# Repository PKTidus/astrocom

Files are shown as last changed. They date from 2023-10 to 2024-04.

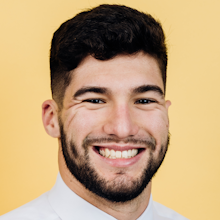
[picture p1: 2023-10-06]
software/website/img/stephen.png

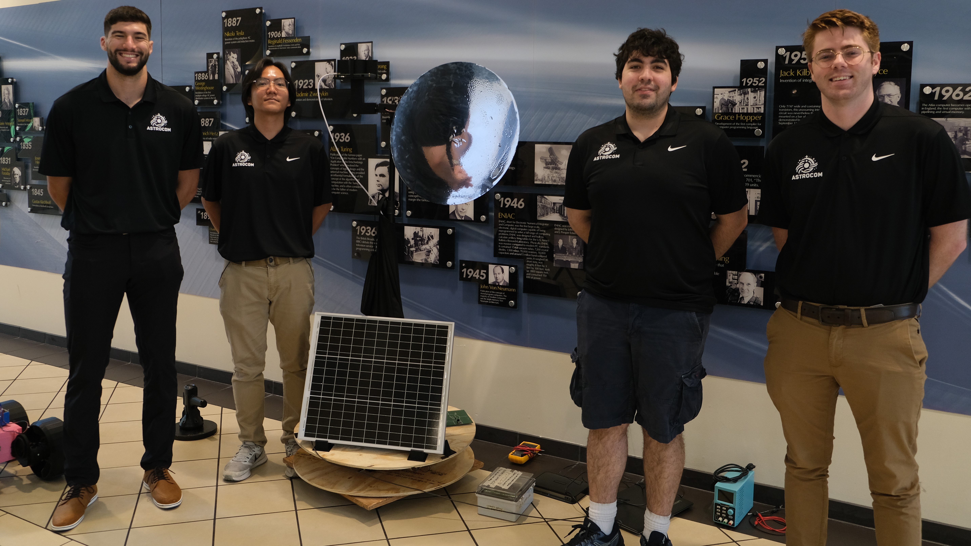
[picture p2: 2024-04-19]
software/website/img/demo_day_pic.jpg

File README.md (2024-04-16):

# A.S.T.R.O.COM. - Advanced Solar Tracking and Rover Observation Communication

The ASTROCOM project, developed in collaboration with the [Florida Space Institute (FSI)](https://fsi.ucf.edu/), addresses the challenge of exploring permanently shaded regions on the lunar surface. Comprising of heliostat and communication beacon towers, ASTROCOM enables wireless transmission of power and information to and from rovers within these shaded areas. The Heliostat tower utilize a reflector to redirect sunlight into the craters, powering solar assets and illuminating shaded regions, while also enabling a communication network. A portable communication beacon, intended to be deployed by rovers, a facilitate communication between the heliostat towers and rovers, overcoming obstacles within the craters.
Heliostat Tower             |  Communication Beacon
:-------------------------:|:-------------------------:
Heliostat Tower CAD  |  Communication Beacon CAD

**Project Members:**  
Alex Fiset (Power/PCB)  
Pedro Kasprzykowski (Wireless/Website)  
Stephen Martin (Sensors/Solar Tracking)  
Binh Pham (Project Lead/Motors)  

**Special Thanks:**  
Dr. Chung Yong Chan  
Dr. Arthur Weeks  

**This project was sponsored by the [Florida Space Institute](https://fsi.ucf.edu/)**  

**This project was made as a [University of Central Florida Electrical and Computer Engineering Department](https://www.ece.ucf.edu/) Senior Design project throughout the Fall 2023 - Spring 2024 term**

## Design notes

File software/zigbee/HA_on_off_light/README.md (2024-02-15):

| Supported Targets | ESP32-C6 | ESP32-H2 |
| --- | --- | --- |

# Light Bulb Example

This test code shows how to configure Zigbee end device and use it as HA on/off light bulb.

The ESP Zigbee SDK provides more examples and tools for productization:
* [ESP Zigbee SDK Docs](https://docs.espressif.com/projects/esp-zigbee-sdk)
* [ESP Zigbee SDK Repo](https://github.com/espressif/esp-zigbee-sdk)

## Hardware Required

* One development board with ESP32-H2 SoC acting as Zigbee end device (loaded with HA_on_off_light example)
* A USB cable for power supply and programming
* Choose another ESP32-H2 as Zigbee coordinator (see [HA_on_off_switch example](../HA_on_off_switch))

## Configure the project

Before project configuration and build, make sure to set the correct chip target using `idf.py --preview set-target TARGET` command.

## Erase the NVRAM

Before flash it to the board, it is recommended to erase NVRAM if user doesn't want to keep the previous examples or other projects stored info using `idf.py -p PORT erase-flash`

## Build and Flash

Build the project, flash it to the board, and start the monitor tool to view the serial output by running `idf.py -p PORT flash monitor`.

(To exit the serial monitor, type ``Ctrl-]``.)

## Example Output

As you run the example, you will see the following log:

light bulb:
```
I (918) ESP_ZB_LIGHT: status: 255
I (901) ESP_ZB_LIGHT: Zigbee stack initialized
I (901) ESP_ZB_LIGHT: Start network steering
I (2611) ESP_ZB_LIGHT: Joined network successfully (Extended PAN ID: aa:98:48:01:a0:03:f7:84, PAN ID: 0x0e8b)
I (5651) ESP_ZB_LIGHT: on/off light set to 1
I (6631) ESP_ZB_LIGHT: on/off light set to 0
I (7331) ESP_ZB_LIGHT: on/off light set to 1
I (8251) ESP_ZB_LIGHT: on/off light set to 0
I (9111) ESP_ZB_LIGHT: on/off light set to 1
I (9671) ESP_ZB_LIGHT: on/off light set to 0
```

## Light Control Functions

 * By toggling the switch button (BOOT) on the ESP32-H2 board loaded with the `HA_on_off_switch` example, the LED on this board loaded with `HA_on_off_light` example will be on and off.

## Troubleshooting

For any technical queries, please open an [issue](https://github.com/espressif/esp-idf/issues) on GitHub. We will get back to you soon.

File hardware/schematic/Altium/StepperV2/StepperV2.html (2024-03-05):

Altium customize

# Board Information Report

Date: | | 2/26/2024
Time: | | 11:22:44 AM
Elapsed Time: | | 00:00:00
Filename: | | C:\Users\binhp\OneDrive\Desktop\Working\School\Senior_Design\Github\astroscom\hardware\schematic\Altium\StepperV2\StepperV2.PcbDoc
Units: | | mmmils

## Contents

Contents

Board Specification

General

## Board Specification

General
Board Size | 4995mils x 4000mils
Components on board | 58

Back to top

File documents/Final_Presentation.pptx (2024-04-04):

## A.S.T.R.O.COM. Advanced Solar Tracking and Rover Observation Communication

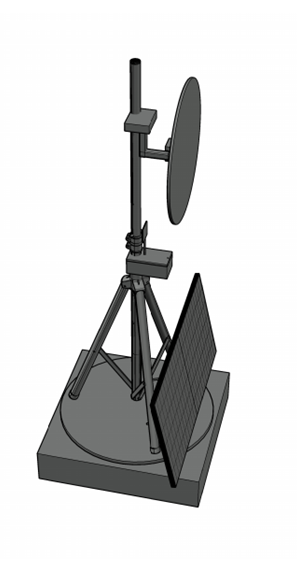
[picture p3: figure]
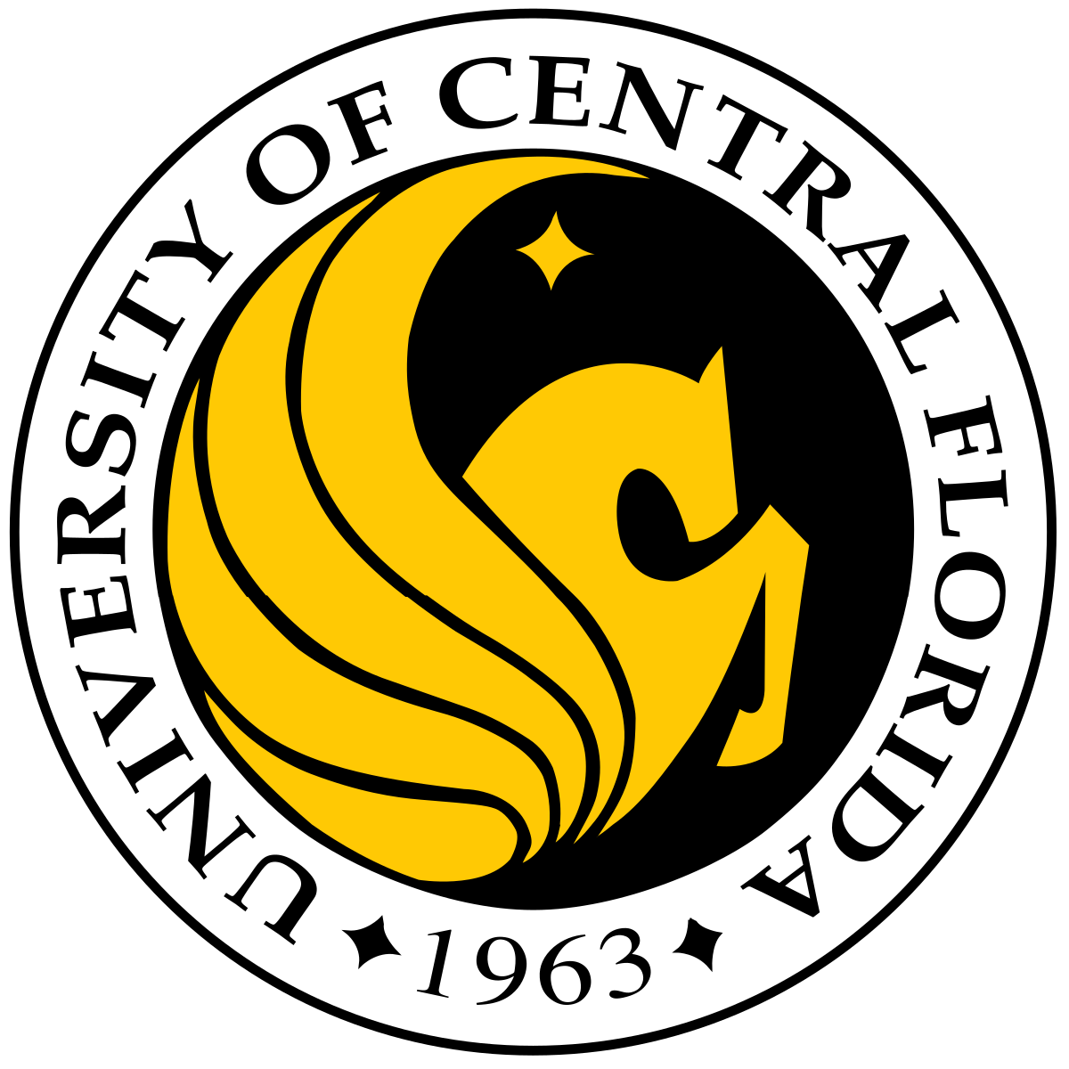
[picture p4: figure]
University of Central Florida - Wikipedia

Alex Fiset | Pedro Kasprzykowski | Stephen Martin | Binh Pham
Electrical Engineering | Computer Engineering | Computer Engineering | Computer Engineering

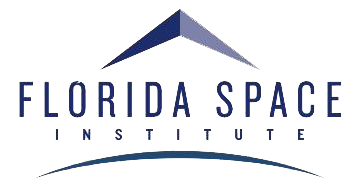
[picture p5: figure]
Florida Space Institute - Wikipedia

Project sponsored by Florida Space Institute (FSI)

## Motivation and Background

- South Pole of Moon is area of interest for researchers
- Lunar south pole has many craters that are in permanent darkness due to the sun's path across the lunar south pole's sky
- Approached by FSI to solve a few problems for lunar exploration:
  1. Permanently dark locations on the moon are difficult to explore
    - Lack of power infrastructure on the moon limits exploration
    - Permanently dark locations are a valuable location for research
  2. Communication on lunar surface is limited
    - Range of communication limits exploration of craters
    - Limited communication infrastructure on moon

## Motivation and Background

- Proposed Solution:
  1. A heliostat tower
    - To reflect light from the sun into permanently dark locations
    - Equipped with communication capabilities
  2. A smaller communication beacon
    - Carriable by rovers
    - Form a communication network with rovers

## Goals

Overall Goals (High Level)
- Build a tower to handle rover communication.
- Build a tower to handle sunlight diversion to targets.
Stretch Goals
- P2P Networking for communication and mirror tower with rovers.
- Wireless charging and/or docking station for communication tower.

## Objectives

Mirror Tower Objectives (Lower Level)
- Identify optimal sun location based on lux value from sensor.
- Receive requests from communication tower using protocols.
- Create a heliostat algorithm to orient towards the target with motors.
- Create a self-sustainable power supply using solar and battery power.
Communication Beacon Objectives (Lower Level)
- Receive requests from target through mesh network protocols.
- Relay requests to mirror tower using communication protocols.
- Create a small and portable tower that can be moved by rovers.

## Specifications Table

Heliostat Tower
Minimum Temperature | -40°C
Reflector
Minimum Reflectivity | 90%
Response Time | 3 minutes
Solar Panel
Minimum Power | 30W during sunlight hours
Maximum Voltage | 24V
Battery
Minimum Lifespan | 2 weeks without sun

Communication Tower
Minimum Network Range | 20m
Communication Rate | 2400MHz
Maximum Current Draw | 500mA
Latency | 1 second
Maximum Power | 5W

  1. A heliostat tower
    - Respond time to change reflection target estimated to be maximum 3 minutes
    - Minimum power can be usage to all component estimated to be 30W
  2. Communication tower
    - Maximum power usage estimated to be 5W

## Hardware Block Diagram

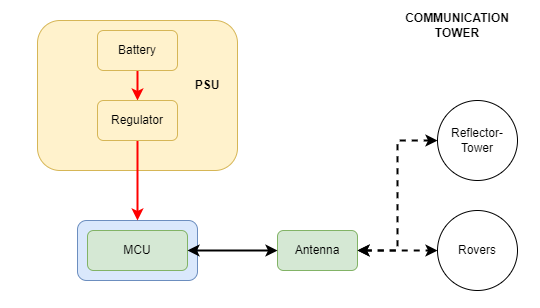
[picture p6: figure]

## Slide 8

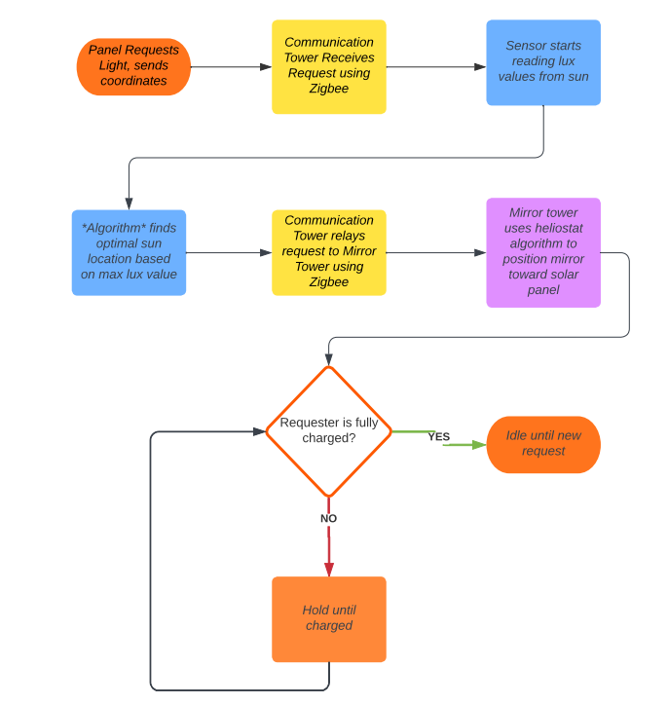
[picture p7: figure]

Software
Block
Diagram

- Fully integrated code software flowchart
  - Perspective of Mirror Tower
  - Yellow is signal from Communication Beacon

## MICROCONTROLLER UNIT

| ESP32 | MSP430 | Raspberry Pi 0 | Arduino MKR1310 | Arduino MK1010
Cost (USD) | 9.18 | 20 | 15 | 46 | 38.6
Zigbee | Yes | No | Yes | No | No
I2C | Yes | Yes | Yes | Yes | Yes
Flash Memory | 4 MB | 128 KB | None | 256 KB | 256 KB
RAM | 520 KB | 2 KB | 512 MB | 32 KB | 32 KB
Power (W) | 1.3644 | 1 | 12.5 | 0.5082 | 0.5082

- Microcontroller was chosen over FPGA
  - Low power consumption, cost, and high amounts of documentation.
- ESP32 is low cost, low power and networking capabilities and all connections required.

## Solar Panels

A monocrystalline 50W panel from Renogy was selected due to the low cost and high performance.

Model | RNG-50D-SS | HQST-50P-US | SP-52-L
Brand | Renogy | HQST | Solbian
Technology | Monocrystalline | Polycrystalline | Monocrystalline
Price | $ 59.99 | $ 65.99 | $ 499.00
Pmax at STC | 50 W | 50 W | 52 W
Voc | 22.3V | 23.3V | 10.9V
Vmp | 18.6V | 19.8V | 9.1V
Imp | 2.69A | 2.53A | 5.7A

## Voltage Regulation

Specifications | Linear Regulators | Switching Regulators
| | Buck | Boost | Buck-Boost
Efficiency | Moderate | High
Heat | Moderate | Low
Voltage Output | Step-Down | Step-Down | Step-Up | Up or Down
Output Ripple | Low | Low | High | Low
Complexity | Low | Moderate | Moderate | High
Cost | Low | Moderate | Moderate | High

Switching Buck regulators were chosen for their simplicity and low cost, being commercially available cheaply from many manufacturers.

## Voltage Regulation

The TPS53JA2 was selected due to the high output current, supported the intended voltage input, and was high efficiency.

Model | LM1085IT-5.0/NOPB | DROK MiniBuck Converter | LM2596 | TPS54JA20
Brand | Texas Instruments | DROK | Texas Instruments | Texas Instruments
Input Voltage | 2.6-26V | 2.5-24V | 3-40V | 2.7–16V
Output Voltage | 3.3 or 5 | 3.3 or 5 | 1.5 to 35 | 0.5 to 5.5V
Output Current | 3A | 3A | 3A | 12A
Price | 2.19 | 1.97 | 1.495 | 0.65
Type | LDO Buck | Buck | Buck | Buck

## Charge Controller

- Two broad categories of Solar Charge Controllers:
  1. PWM
    - Basic pulse width modulation
    - Lower efficiency
    - Cheaper
  2. MPPT
    - Tracks highest power producing operating point
    - Higher efficiency
    - Typically, more expensive

## Charge Controller

The SR11004 from SMARAAD offered the right voltage output, and was compatible with the selected battery chemistry for the lowest price.

Model | BQ25798RQMR | SR11004 | Adventurer
Brand | Texas Instruments | SMARAAD | Renogy
Input Voltage | 24V max | 26V max | 50V max
Output Voltage | 18.8V max, Programmable | 12/24V | 12/24V
Output Current | 5A | 10A | 30A
Price | 6.25 | 39.99 | 59.99
Power | Not Specified | 260W | 1500W
Type | MPPT | MPPT | PWM

## Reflectors

- Material Chosen to fabricate:
1. Aluminum: high heat resistance, durable, and high reflectivity in the moon environment.
2. Mylar: increase reflectivity, high heat change resistance, won’t crack, and don’t reduce quality of refection
- Proof of concept: Acrylic panel as cheaper alternative and easier to fabricate.

## Motors

1. Stepper motor: Nema 23 robustness and strong torque to control the rotation of the whole tower. Can be used on DC system
2. Servo Motors: a cheaper alternative for smaller part movements.
- Incorporated gearbox to increase movement range and control for stepper motor.

Types of Motors | AC | Stepper | Servo
Financial Cost | $200-$2,000 | $20-$200 | $10-$50
Torque | 203000Ncm-610000Ncm | 10-10000Ncm | 10-1000Ncm
Speed | 1800-3600 rmp | Low | High
Voltages requirement | 115V/208V/230V | 3V-100V | 3V-100V
Durability | High | High | Low

## Motor Controllers

1. Stepper Controller TB6560-V2, cheap and can handle the at least 2 amperage from Nema23
2. PCA9685 PWM: Design specific for servo and can control all three servos planned in the system

Controller Models | DRV8434S, 2A Max. | TB6560 | Stepper Motor Driver 36v4 | HiLetgo PCA9685
Cost (USD) | $12.95 | $11.39 | $29.95 | $9
continuous current (A) | 1.2 | 3.5 | 4 | 3A
Micro stepping | 1/256 | 1/16 | 1/256 | I2C
Operating Voltage (V) | 4.5-48 | 10-35 | 8-50 | 5-10

## Batteries

- The battery selected was a Howell Energy LiFePO4 battery.
  - Higher amp hours
  - Lower weight
  - Smaller size
  - Higher price

Model | ML5-12 | HW-4F7 | PQ12V/6AH
Brand | Mighty Max Battery | Howell Energy | Power Queen
Voltage | 12 | 12 | 12.8V
Amp Hour | 5 | 7 | 6
Technology | SLA AGM | LiFePO4 | LiFePO4
Price | 16.99 | 32.99 | 19.59
Charging Requirements | CV | CC 3.5A, CV 14.6V, Built-in BMS | Not Specified, Built in BMS

## Antenna

- The combination of the certain gain range, circular polarization, high-efficiency and wideband characteristics made patch and helical antenna types the ideal choices.
- The PC140’s circular polarization while also being above average in gain and efficiency made it the preferred antenna product.
- The sponsor chose for us to replace the antenna with their choice of the wlaniot.

| PC140 | WPC.25A | FXP74 | PC17 | FXP70
Avg Gain (dB) | -1.92 | -1.14 | -2 | -3.6 | -2
Peak Gain (dBi) | 1.67 | 5.15 | 4 | .9 | 1.1
Efficiency (%) | 64 | 76.9 | 50 | 44 | 63.7
VSWR | <2 | <2 | <2 | <1.5 | <1.5
Polarization | RHCP | Linear | Linear | Linear | Linear
Cost (USD) | $27.26 | $9.21 | $7.69 | $16.60 | $27.09

## Sensor

Sensor Final 4 Options:
- VL6180X and SI1145 include IR which is not needed
- MAX44009 only has breakout board; does not work for PCB
- VEML7700 best choice for price/ability

| VL6180X | MAX44009 | SI1145 | VEML7700
Cost (USD) | $14.49 | $5.96 | $9.95 | $4.95
Measuring Principle | TOF/IR Laser Photodiode | Photodiode | IR-LED Photodiode | Photodiode
Max Lux | 100000 | 188000 | 128000 | 120000
Ambient Light Sensing | Yes | Yes | Yes | Yes
Operating Current (mA) | 0.3 | 0.003 | 7 | 0.045
I2C | Yes | Yes | Yes | Yes

## Development Environment: Languages and Repositories

Programming Languages
- C: best choice for MCU programming, low-level
- Java: best for object-oriented programming, low-level
- Python: best for existing libraries, high-level
Choice: C
Repositories
- GitHub: most popular repo, widely used among many software devs
- Bitbucket: Git based repo, includes task scheduling and team goal software
Choice: GitHub

## Vectoring and Positioning / Solar Tracking Algorithm

1. Heliostat algorithm chosen as it is open source and availability. Good capability with ESP32-C6 and C language

Algorithms | Heliostat | Kalman Filtering | Ray Tracing
Financial Cost | Open Source | Ambiguous | Not available
Sensor | Ambient Light | Ambient Light | Ambient Light
Algorithm code library | Available on GitHub | Available in python | Available in Research paper
Efficiency | High | Low | Medium
MCU compatibility | Good (C Language) | Fair (Python) | Good (C Language)

## Communication technologies

- The combination of low power consumption, suitable range, options for frequency and high scalability made Zigbee the ideal communication technology to implement.

Criteria | Wi-Fi | Bluetooth | Zigbee | Z-Wave
Range (m) | 45 | 10 | 980 | 800
Data rate | 54 Mbps | 1 Mbps | 250 Kbps | 100 Kbps
Power consumption | 30 uA-250 mA | 9 uA-39 mA | 12 uA- 54 mA | 1 uA-23 mA
Max devices | 255 | 3-4 | 100 | 232
Scalability | ✓ | ✖ | ✓ | ✓
Frequency | 2.4/5/6 GHz | 2.4 GHz | 915 MHz/2.4 GHz | 908-916 MHz

## Hardware Design

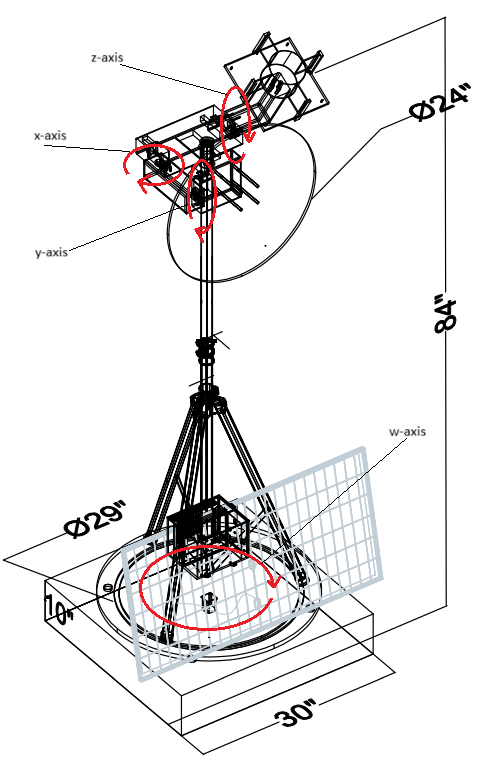
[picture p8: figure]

- Design two separate towers, each with their own design constraints
- Majority of focus is on heliostat tower, as it is more complex
- Schematics and PCB designs
- Heliostat structure
- Tripod on a "Lazy Susan"
- Communication Beacon
- Antenna on an enclosure

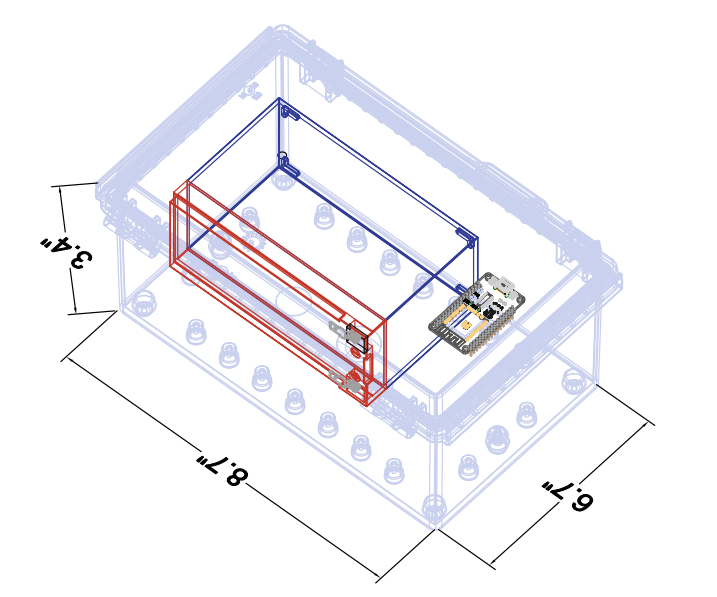
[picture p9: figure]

## Power Delivery/ Electrical Power System

## Servo Motor Controls

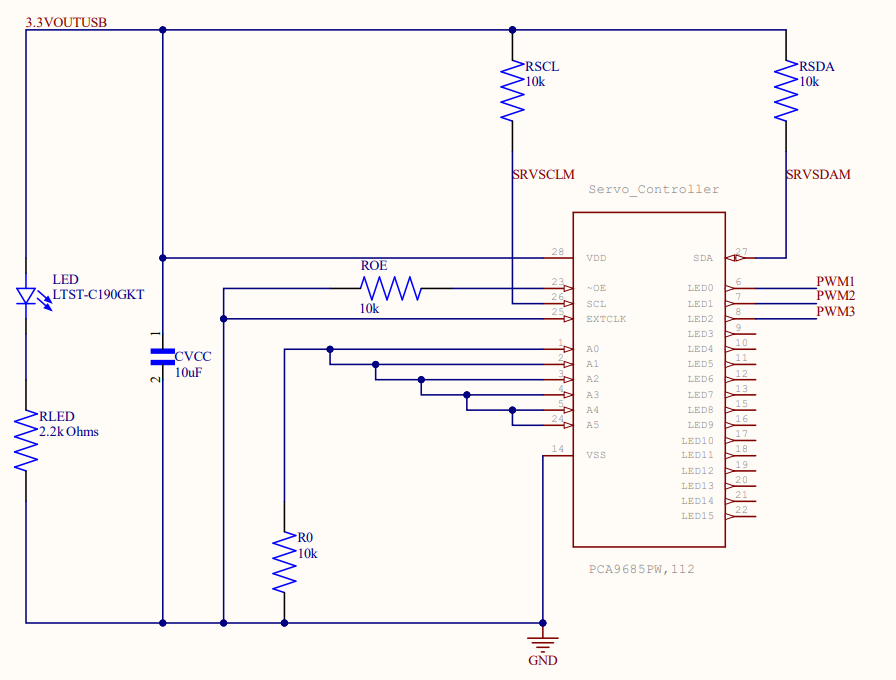
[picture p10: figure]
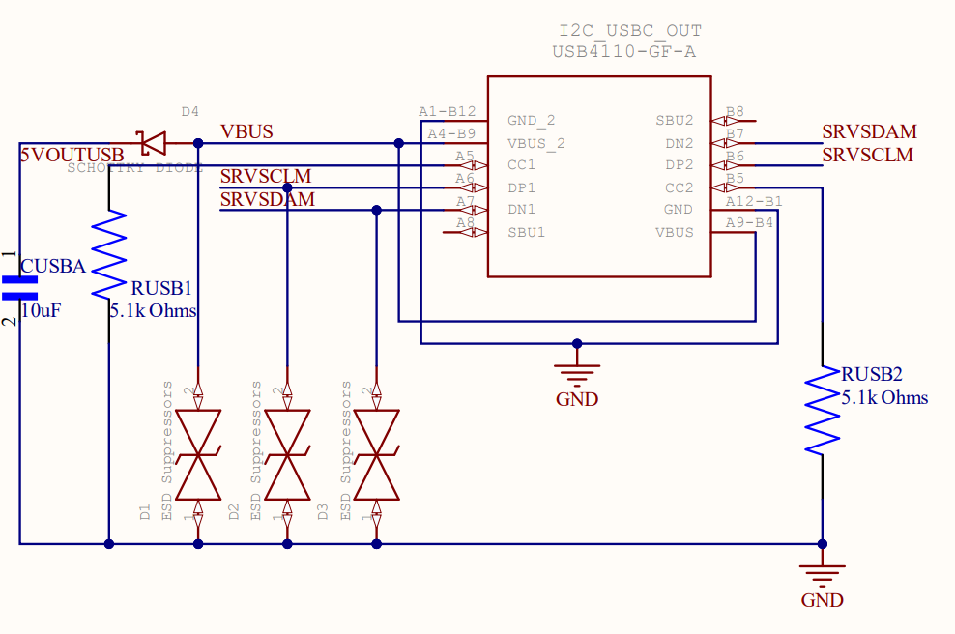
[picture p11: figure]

## Sensor Control

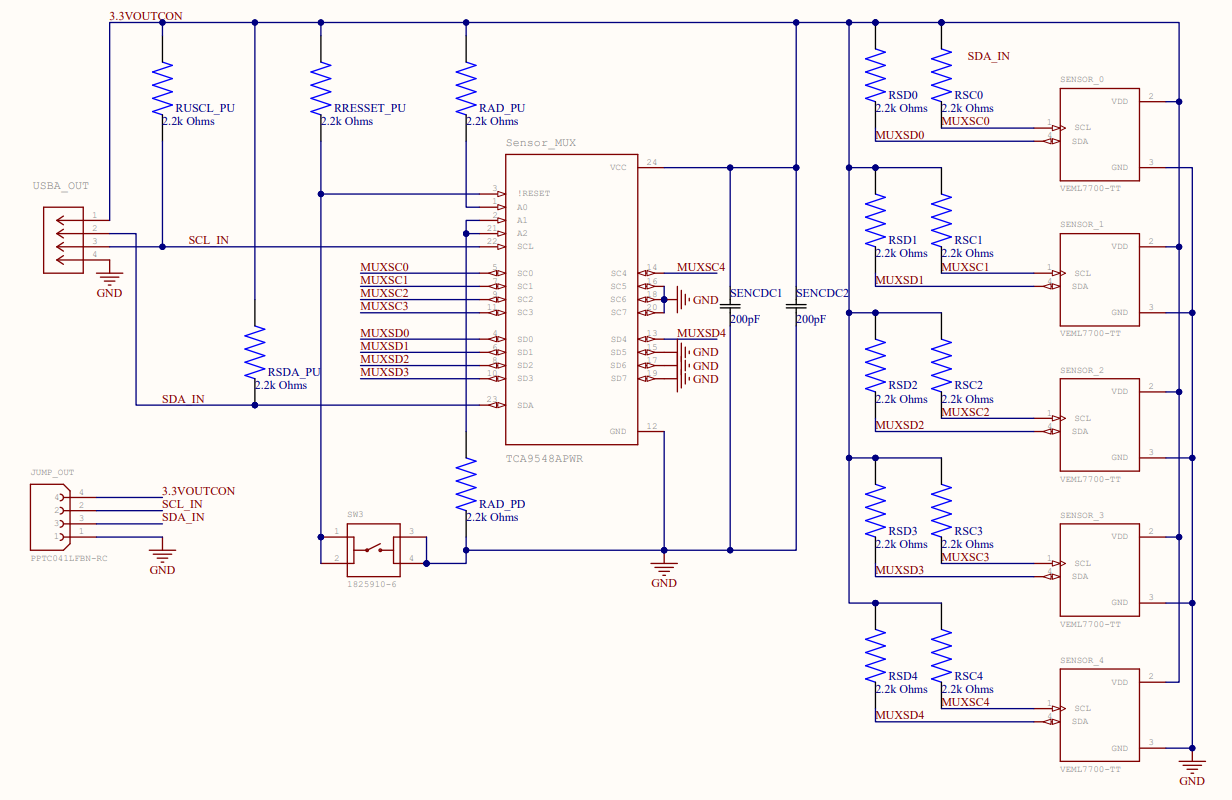
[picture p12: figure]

## MCU System

## Lower-Level Subsystem

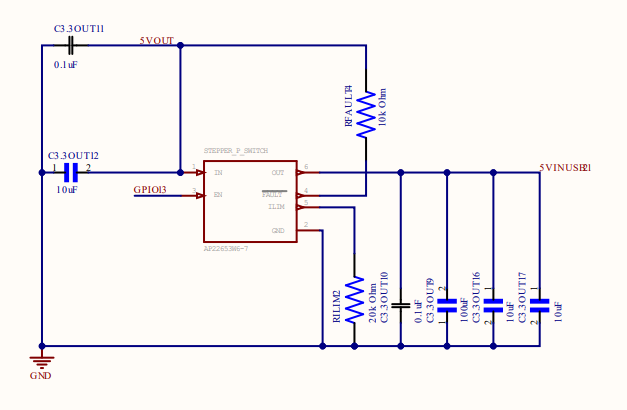
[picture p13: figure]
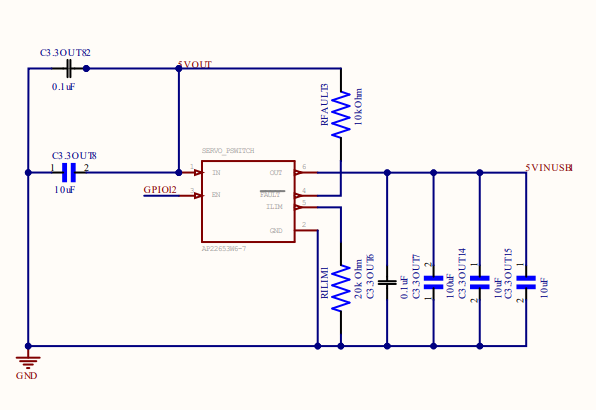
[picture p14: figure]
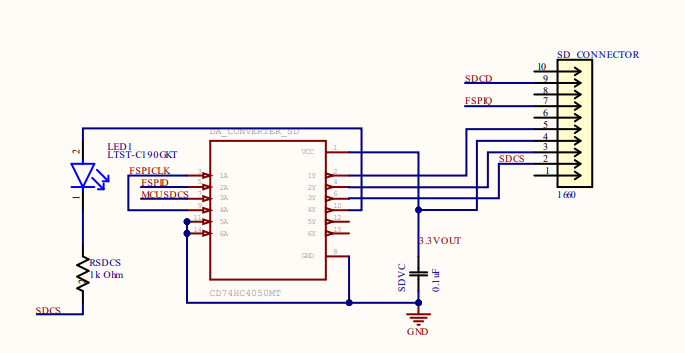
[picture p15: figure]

## Lower-Level Subsystem

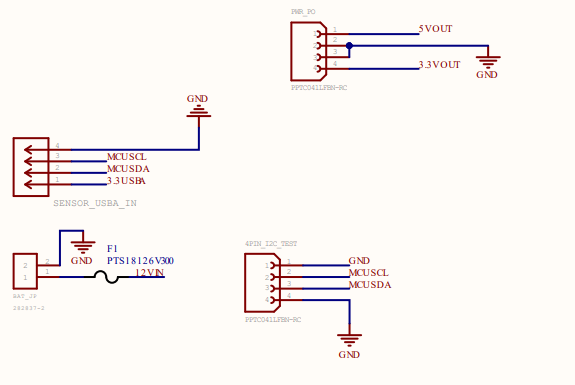
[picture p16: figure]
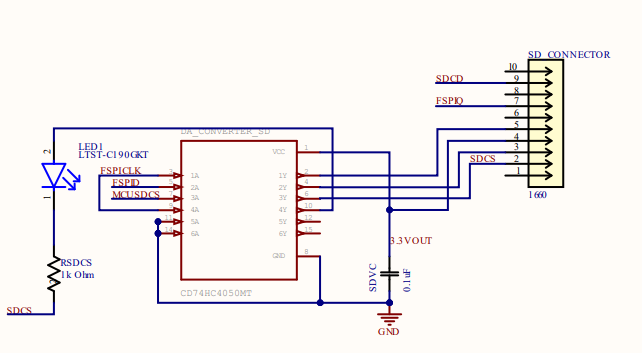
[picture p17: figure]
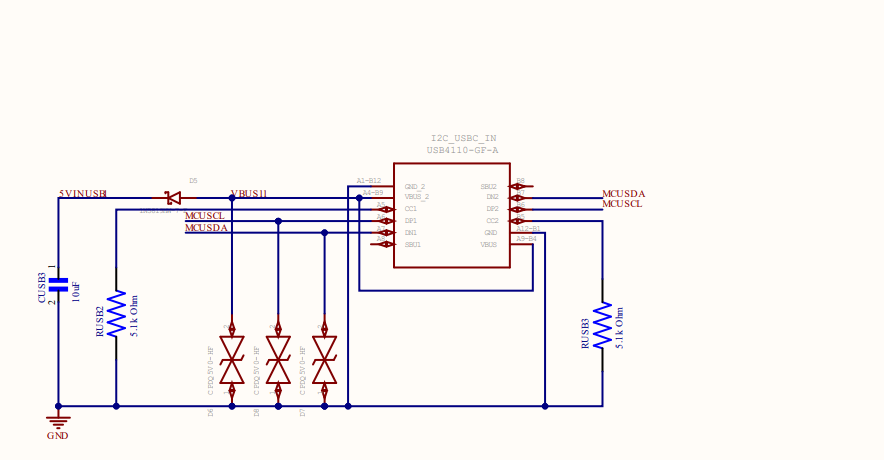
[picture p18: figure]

## Power Control Algorithm

Component | Essential/Non-Essential | Low-Power Considerations
MCU | Essential | Low-Power Mode, only essential functions
Antenna | Essential | Receive only
Sensors | Essential | Sensors will be turned on periodically
Stepper Motor | Non-Essential
Servo Motors | Non-Essential

- Goal was to reduce power consumption when the sun would not be visible
- Reducing usage of non-essential components during these times would preserve battery charge

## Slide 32

MCU PCB

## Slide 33

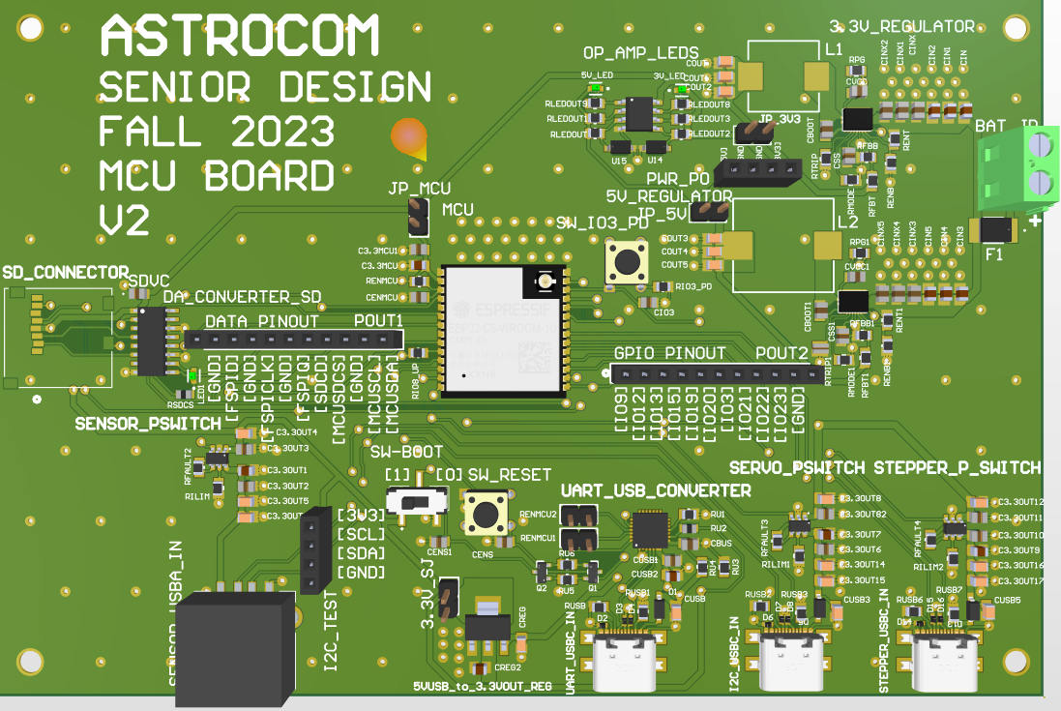
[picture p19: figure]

MCU PCB

## Sensors PCB

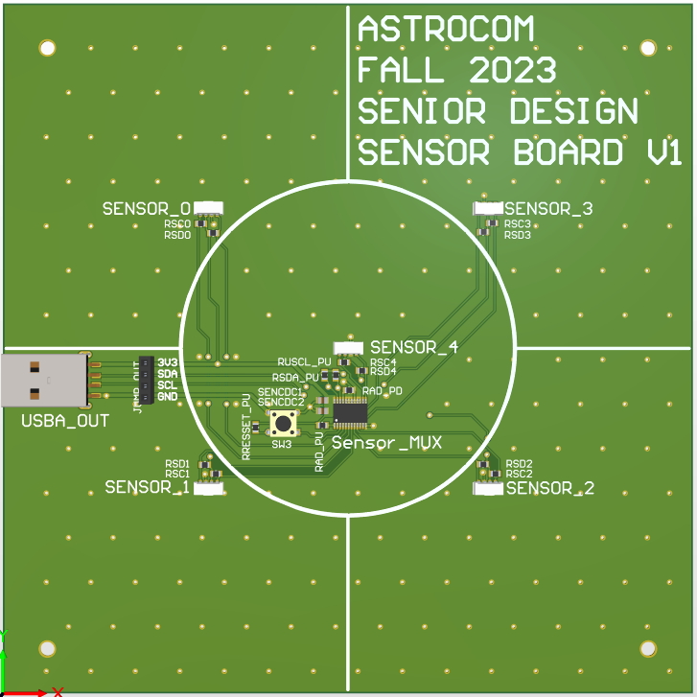
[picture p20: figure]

## SErVo Motor controller PCB

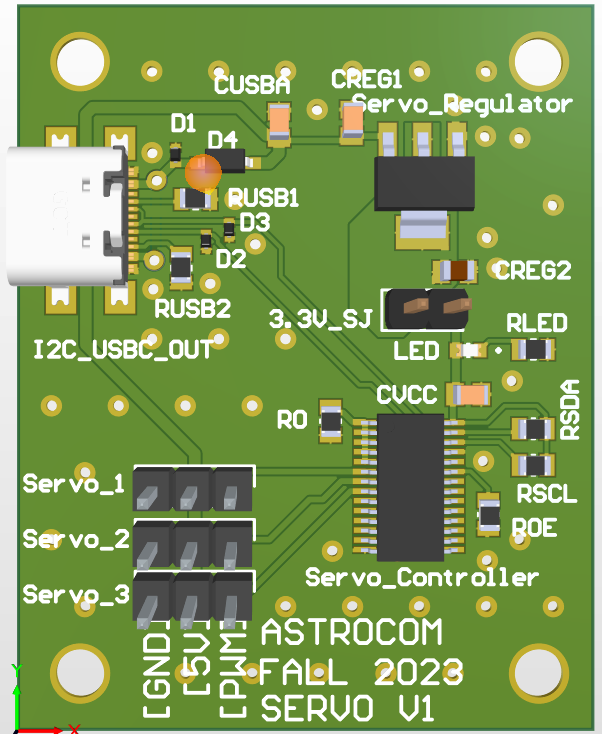
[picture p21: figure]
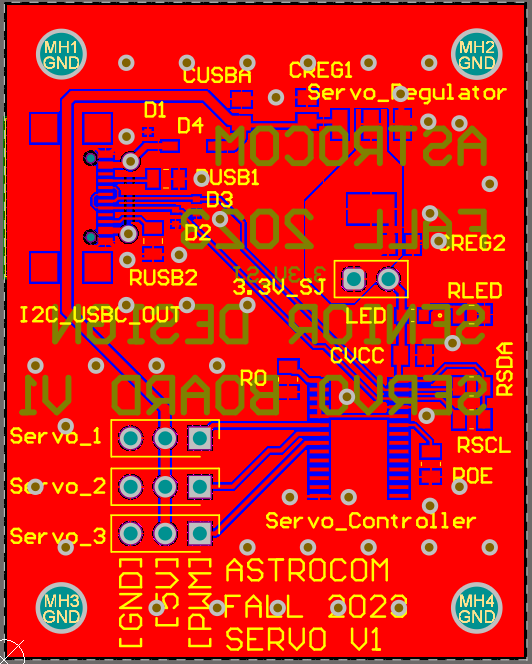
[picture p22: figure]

## Software Design

- Details on software design for the overall system which includes:
- Communications through the mesh network
- Collecting sensor information
- Positioning reflector to deliver sunlight to target
- Represented with software diagrams

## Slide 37

Case
Diagram

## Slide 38

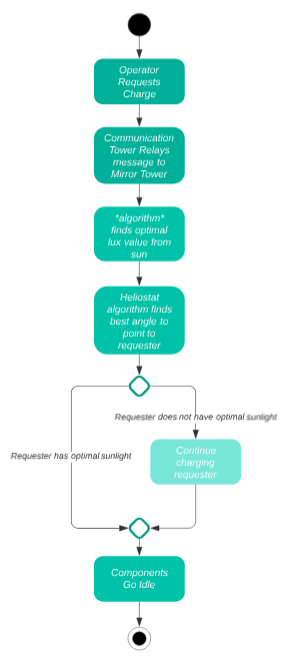
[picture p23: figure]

Activity Diagram

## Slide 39

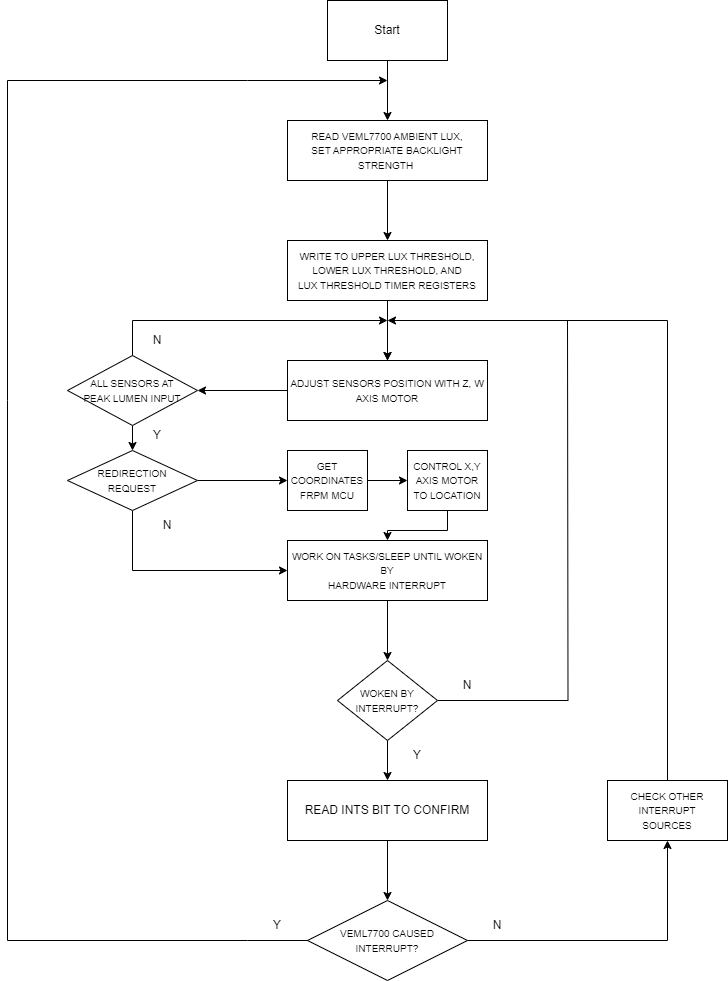
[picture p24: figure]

Motor positioning of Reflector based on light intensity algorithm.

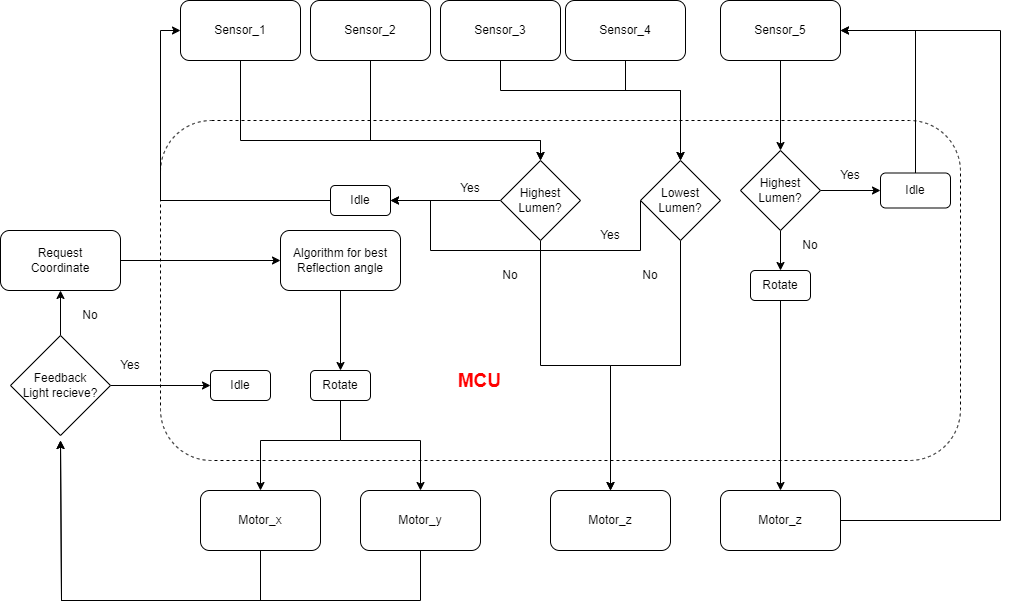
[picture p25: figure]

## Hardware testing

- Tested components and had great success.
- Did have a few issues during implementation including:
  - Strapping pins and UART TX/RX mix-ups
  - Higher than expected channel capacitance causing low rise time for I²C
  - Voltage drop from servos, resetting the servo controller
- These issues were resolved with a mix of software and hardware changes.

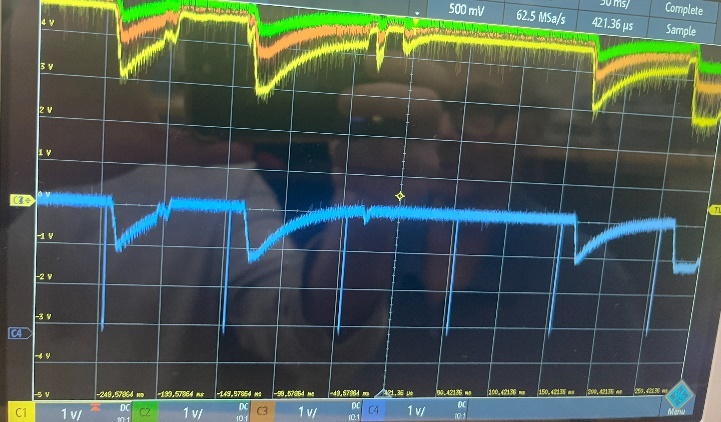
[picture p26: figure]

## Software testing

- Transforming individual parts code to integrated code
  - Included interrupts to handle events
  - Sensors in certain locations are averaged and divided by each other to dynamically track movements
  - Scaling operations were needed to transform step sizes from different servos
  - Zigbee operations included to switch targets
- Created our own coordinator for testing but will use rover from G16 in live demo
  - This coordinator will relay information from communication box (Zigbee end device) to the reflector tower (Zigbee end device)

## Administrative Contents

Electrical Engineering | Responsibilities
Alexandre Fiset | PSU Design and Implementation
| PCB Design
| MPPT Tracking Implementation
| Administrative Documentation
Computer Engineering | Responsibilities
Binh Pham | Reflector Technology and Design
| Motor and Motor Controls
| Vectoring Technology
| Project Lead
| Positioning and Vectoring Algorithm
Computer Engineering | Responsibilities
Pedro Kasprzykowski | MCU Selection and Implementation
| Software Design and Implementation
| Antenna and Communications
| Website Design and Management
Computer Engineering | Responsibilities
Stephen Martin | Sensor Selection and Implementation
| MCU Selection and Implementation
| Positioning and Vectoring Algorithm
| Software Design and Implementation

## Mechanical's Budgets

Component | Name | Price/unit | Quantity
Mirror | 0.032" x 24" x 24", 3003-H14 Aluminum Sheet | $28.86 | 1
Mirror Coating | Mylar Sheet | $25.99 | 1
Frame | ADJ LTS-6 T-Bar Tripod Lightweight Lighting Stand | $54.99 | 1
Base Panels | Plywood Panels 4ftx8ft | $25.60 | 2
Communication Tower Box | Junction Box | $26.89 | 1
Wheel Hub Bearing | Rear Wheel Hub | $44.90 | 1

## Electrical’s Budget

Component | Name | Price | Quantity
Battery | Howell Energy hw-4f7 | 32.99 | 1
Motor w | Nema 23 | $30.73 | 1
Motor x-y-z | 9.5-11kg*cm Servo Motor | $17.59 | 3
Charge Controller/BMS | Smaraad SR11004 | $39.99 | 1
Solar Panel | RNG-50D-SS | $49.99 | 1
Microcontroller | ESP32-C6-DEVKITC-1-N8 | $9.00 | 1
External Antenna | Wlaniot 2.4G | $17.98 | 2
MicroSD card | 5251 | $4.50 | 2
MicroSD card breakout board+ | 254 | $7.50 | 1

## PCB’s Budget

Component | Name | Price | Quantity
Microcontroller for PCB | ESP32-C6-WROOM-1U | $3.48 | 1
Stepper Motor Controller | DRV8833PW | $2.84 | 1
Servos Motor Controller | PCA9685PW,112 | $2.64 | 1
3.3V Regulator | TPS54JA20 | $1.50 | 1
5V Regulator | TPS54JA20 | $1.50 | 1
USB-A Connector | 2057-USB-AP-S-RA-SMT-ND | $0.55 | 3
Sensor-MUX | TCA9548APWR | $1.78 | 1
Sensor | VEML7700 | $1.88 | 5
USB-to-UART Bridge Controller | CP2102N-A02-GQFN28 | $4.07 | 1
MicroSD Socket | 1660 | $1.95 | 1
Misc. | Resistors, Capacitors, Inductr, Jumpers, Etc.…. | ~$20.00

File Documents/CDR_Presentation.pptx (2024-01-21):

## A.S.T.R.O.COM. Advanced Solar Tracking and Rover Observation Communication

Group 14’s
Members:


Alex Fiset | Pedro Kasprzykowski | Stephen Martin | Binh Pham
Electrical Engineering | Computer Engineering | Computer Engineering | Computer Engineering

## Motivation and Background

## Goals & Objectives

## Specifications Table

Heliostat Tower
Minimum Temperature | -40°C
Reflector
Minimum size | 1ft diameter
Maximum size | 5ft diameter
Maximum Weight | 9kgs
Minimum Reflectivity | 90%
Response Time | 3 minutes
Tower Frame
Maximum total weight | 27kgs
Minimum Weight Capacity | 10kgs
Solar Panel
Minimum Power | 30W during sunlight hours
Maximum Voltage | 24V
Battery
Minimum Lifespan | 2 weeks without sun

Communication Tower
Minimum Enclosure Volume | 6.5"x6.5"x5"
Maximum Weight | 2kg
Minimum Network Range | 20m
Communication Rate | 2400MHz
Voltage input | 3.3V or 5V
Maximum Current Draw | 500mA
Minimum Temperature | -40°C
Latency | 1 second
Maximum Power | 5W

## Hardware BlockDiagram


## Software BlockDiagram


## Comparison and Selection of Hardware

## MCU

## Solar Panels

## MCU

## Voltage Regulation

## Charge Controller

## Reflectors

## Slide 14

## Comparison and Selection of Software

## Hardware Design

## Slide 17

## Software Design

## PCB Design

## Stepper Motor Controller PCB


## MCU PCB


## SErVo Motor controller PCB


## Sensors PCB


## Administrative Contents

## Overall Budget and Financing

Sub-System | Budget | Sponsor | Additional Budget
PSU and Solar | $ 150.00
Frame/Reflector | $ 200.00
PCBs and Electrical | $ 100.00
Total | $ 450.00

## Mechanical's Budgets

Component | Name | Price/unit | Quantity
Mirror | 0.032" x 24" x 24", 3003-H14 Aluminum Sheet | $28.86 | 1
Mirror Coating | Mylar Sheet | $25.99 | 1
Frame | ADJ LTS-6 T-Bar Tripod Lightweight Lighting Stand | $54.99 | 1
Base Panels | Plywood Panels 4ftx8ft | $25.60 | 2
Communication Tower Box | Junction Box | $26.89 | 1
Wheel Hub Bearing | Rear Wheel Hub | $44.90 | 1

## Electrical’s Budget

Component | Name | Price | Quantity
Battery | Howell Energy hw-4f7 | 32.99 | 1
Motor w | Nema 23 | $30.73 | 1
Motor x-y-z | 9.5-11kg*cm Servo Motor | $17.59 | 3
Charge Controller/BMS | Smaraad SR11004 | $39.99 | 1
Solar Panel | RNG-50D-SS | $49.99 | 1
Microcontroller | ESP32-C6-DEVKITC-1-N8 | $9.00 | 1
External Antenna | Wlaniot 2.4G | $17.98 | 2
MicroSD card | 5251 | $4.50 | 2
MicroSD card breakout board+ | 254 | $7.50 | 1

## PCB’s Budget

Component | Name | Price | Quantity
Microcontroller for PCB | ESP32-C6-WROOM-1U | $3.48 | 1
Stepper Motor Controller | DRV8833PW | $2.84 | 1
Servos Motor Controller | PCA9685PW,112 | $2.64 | 1
3.3V Regulator | TPS54JA20 | $1.50 | 1
5V Regulator | TPS54JA20 | $1.50 | 1
USB-A Connector | 2057-USB-AP-S-RA-SMT-ND | $0.55 | 3
Sensor-MUX | TCA9548APWR | $1.78 | 1
Sensor | VEML7700 | $1.88 | 5
USB-to-UART Bridge Controller | CP2102N-A02-GQFN28 | $4.07 | 1
MicroSD Socket | 1660 | $1.95 | 1
Misc. | Resistors, Capacitors, Inductr, Jumpers, Etc.…. | ~$20.00

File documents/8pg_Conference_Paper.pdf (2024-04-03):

# Advanced Solar Tracking and Rover Observation Communication

A.S.T.R.O.COM.

### Alex Fiset, Pedro Kasprzykowski, Stephen Martin, Binh Pham

### Dept. of Electrical Engineering and Computer

Science, University of Central Florida, Orlando,

### Florida, 32816-2450

### Florida Space Institute Orlando, Florida, 32826

Abstract | — | The ASTROCOM project, developed in
collaboration the Florida Space Institute (FSI), addresses the challenge of exploring permanently shaded regions on the lunar surface. Comprising heliostat and communication beacon towers, ASTROCOM enables wireless transmission of power and information to and from rovers within these shaded areas. The Heliostat tower utilize a reflector to redirect sunlight into the craters, powering solar assets and
illuminating shaded | regions, | while | also | enabling a
communication network. A portable communication beacon, intended to be deployed by rovers, a facilitate communication between the heliostat towers and rovers, overcoming obstacles within the craters. This document outlines the design process,
technologies, | implementation, | and | testing | results | of
ASTROCOM.
Index Terms — Fresnel reflection, motor coordination, wireless mesh networks, solar panels, solar energy, batteries
I. INTRODUCTION

ASTROCOM marks a significant advancement in space exploration technology, presenting a sophisticated solar reflector system integrated with a mesh network communication protocol. This project aims to enhance energy harnessing and communication capabilities in extraterrestrial environments. By delving into the detailed design and implementation of ASTROCOM, this paper sheds light on its components, testing procedures, and potential for further improvement.
At the core of ASTROCOM lies a blend of advanced technologies meticulously crafted to tackle the challenges of space exploration. By combining state-of-the-art hardware components with sophisticated software algorithms and Zigbee communication protocols, ASTROCOM offers efficient solar tracking and seamless communication across vast distances in space. As subsequent sections unravel the system's architecture and operational intricacies, ASTROCOM highlights the role of innovation in pushing the boundaries of space exploration, promising new capabilities for future missions beyond Earth.

II. OVERVIEW

This paper serves to provide a description of ASTROCOM project. The system components are first summarized in III, then the hardware and software implementation are discussed in IV and V. Following is the discussion of the changes made during testing in VI, and final conclusions presented in VII.

III. SYSTEM COMPONENTS

The overall system can be broken down into parts for further explanation of the entire project. The following parts that were designed or purchased compose the entire system.

### A. MCU

The ESP32-C6 microcontroller serves as the main control center of the system with its dual core processor and ample flash memory. The chip also has on board Zigbee communication. These aspects allow the microcontroller to balance handling all the various library dependencies within the code and running several motors in accordance with light sensor readings and being attached to the Zigbee network so that commands may be received and sent [1].

### B. Voltage Regulators

The TPS54JA20 IC regulator used is a small high-efficiency synchronous buck converter. Two of these regulators were used to step down the 12V supply from the charge controller down to 5V and 3.3V for the MCU, servos and other peripherals. This small IC has proven to be a powerful regulator and runs cool even under high loads. The regulator offers high efficiency, which is ideal in the context of space exploration and renewable energy. This IC can provide a maximum of 12A, which is more than sufficient for the systems supplied [2].

### C. Solar Panel

The Renogy RNG-50D-SS, a 50W rated panel, was used to ensure a power surplus during standard operation. The combination of low price, weight, and high-power output, reliability and performance in low-light conditions made it effective. Additionally, the availability of detailed datasheets and IV curve data for the Renogy panel benefited the project during testing. The panel is rated for 50W, providing a Voc of 22.2V and an Isc of 2.9A. At the optimum power point the panel operates at a Vmp of 18.6V and an Imp of 2.6A [3].

### D. Charge Controller

SMARAAD’s SR11004 charge controller was used for the project. The charge controller offers charge control modes for different battery chemistries. The charge controller also supports up to 30A at 12V through the device. This device serves to charge the LiFePo battery and step down the voltage from the solar panel to provide a steady 12V for the stepper and the 5V and 3.3V regulators.

### E. Battery

The batteries used for ASTROCOM are 2 12V 7Ah LiFePo4 batteries from Howell Energy. One is utilized to provided power for the communication beacon, and the other serves to provided power for the heliostat during low-light conditions. The battery has its own internal BMS, which prevents over and under voltage conditions. This is beneficial during testing to increase safety and reduce risk of improper charging. The 7Ah supplied is more than enough for both systems, as the communication beacon has very little power draw by design, and the heliostat will draw power from the solar panel for the vast majority of operation.

### F. Light Sensors

The VEML7700 light sensors were used on our sensor board due to its superior performance across various criteria, such as high lux value, low power consumption, and compact size, all of which are essential for our project requirements. Its high maximum lux value of over 100,000 is particularly crucial as it allows for precise positioning of the mirror to optimize solar energy absorption. The current draw is a minimal 0.45mA which allows for battery power to be saved during operations. Lastly, the overall size of the sensor can be measured by the area which is a minute 15.98mm²
[4].

### G. Motors and Motor Drivers

Three DS3225 servo motors control the x and y axis of the mirror for light reflection; and the vertical rotation of sensors to tracing sun light. Servos have high torque compared to its small size and have accurate precision for light weight components. The w axis rotation of the whole tower is heavier, which requires a NEMA 23 stepper motor, and the precision of rotation are not a requirement.
A PCA9685 chip controls all servo motors through I2C communication bus. The chip switching the required PWM to rotate each servo into a calculated position by the ESP32-C6 MCU. Through calculations a SPI signals output to TB6560 chip to control the stepper motor. To operate with high torque, the stepper required above 2A, which TB6560 provide along with 24V rating [5].

### H. Mechanical Parts

A plate of polymethyl methacrylate was cut in to a 2 ft diameter circle to perform as a mirror backing due to the high stability and flexibility. Then a layer of mylar applied on top using adhesive to give a reflective surface to reflect sun light. The reflector attaches to a housing and arm to be control by servo motor in vertical and horizonal axis.
Five sensors were used to calculate the direction of sun light; hence a partition is needed to distinguish the amount of light at each sensor. The sensor board divided into five sections, the peripheral quadrant used to find the left, right, up and down ray tracing. The middle section used to confirm the direct sunlight ray input.


Fig. 1. Sensor’s partition design and measurement.

Multiple board’s housings used to contain MCU, stepper and servo controller PCB boards. The housing of stepper contained air vent for heat dissipation from heat sink due to the high amperage pull from the stepper motor. Further development of fan implementation can be attached directly on to the housing box.
The reflector tower’s base is made from 3 sheets of 3/8ths inch plywood. It features a “lazy-susan” turntable bearing to enable the tower to rotate freely. To prevent balance issues, roller bearings were placed between the base of the turntable and the top of the base. The base also stores the stepper motor, geared 2-1, to reduce the torque required from the stepper. A 4-conductor slipring is utilized to transfer signals down to the stepper without the cabling twisting. 3D printed components such as the gears, stand, and housings, helped reduce the total cost of the project and enabled iterative design.
The communication beacon is an enclosure is an IP65 rated enclosure, which stores a Howell Energy LiFePo battery, 12-5V regulator and ESP-C6 Devkit board. The plastic enclosure ensures that the Zigbee communication is unimpeded and keeps the internal components free from dust or humidity during testing.

### I. Wireless Communication Protocol

Zigbee was used to implement the mesh network in the project. While supporting theoretically infinite scalability with the addition of more router devices, Zigbee is also low power and provides outstanding range on a location like the moon. The communication rate is not a worry, reliability is preferred. Zigbee provides the backbone for a stable, reliable and scalable mesh network between rovers, towers and any additional nodes on the moon’s surface [6].


Fig. 2. Reflector Tower design and measurements; Including a base with lazy Sussan design, boards housing at the bottom, solar panel, tripod, top board housing. Four rotation axis w, x, y and z are labeled.

IV. HARDWARE


Fig. 3. Overall hardware diagram

### A. Reflection control

The heliostat reflection angle can be calculated using an algorithm; according to Figure 4 and information from Alberto [7], we can realize (1) such that:


Fig. 4. Reflection of light diagram, the Horizon would represent a mirror surface.

d
r

= |
sin((
x

2n+2))φ

sin((
x−2n+1
2n+1

)φ )

|. | (1)

This is based on the law of sine to calculate the angle, TCB at the center of the reflection circle, φ is the rotation origin, and T is the target location. The angle variable θ is unknown and can be calculated using geometry such that φ
2
is the limit of an iterative process.
An algorithm can be realized as (3), with n being the rotating process iteration. This algorithm is the base to find the highest angle of the lumen to the reflector. However, the mirror needs to be rotated in 2 different axes based on incoming requests rather than automatically shine to a fixed position—an additional algorithm based on the grid network to pinpoint a location.
An additional algorithm of rotation needs to be used to control the reflector. The horizontal axis W of the whole tower will rotate according to the sun's position. An additional motor must turn the mirror to control the X and Y axis to point to a pre-determined location based on the network algorithm [8].

d
r

=

sin (θ)
sin (2θ−φ)
. | (2)

### B. The PCB Design

For ASTROCOM, four unique PCBs were designed: an MCU board, servo controller board, sensor board, and stepper board.

1) MCU: The most complex was the MCU board. The MCU board was designed to interact with four different devices: the sensor board, the servo controller board, the stepper controller and a laptop for programing. This required five connectors, four for the peripheral devices and one for the 12V line from the charge controller. For the laptop connector, a USBC connector and a USB/UART converter were utilized. Also included on this connector was a 5V to 3.3V regulator with a jumper bridge, enabling the 3.3V line to be powered directly from the laptop without external power supply during testing. This proved useful and special attention was paid to avoid connecting the 5V lines from the USBC and the board’s 5V line, as well as avoiding connecting both 12V to 3.3V regulator and the 5V to 3.3V regulator simultaneously, to avoid unbalanced loading. The stepper and servo connectors utilized USBC connectors as well but did not use the USB protocol. USBC connectors were chosen over other USB connectors because of the higher power delivery capabilities of the connector. This enabled the utilization of cheap commercially available connectors without the overhead of components required for the USB protocol. The servo controller on the servo board was instead communicated to using I²C, and delivered 5V, through a power switch IC enabled with a GPIO. The utilization of power switch ICs allowed the the peripheral boards to be de-powered, reducing the power draw from those components when not needed. Likewise, the stepper controller board was intended to be connected via USBC, sending the direction and clock data directly to the stepper controller over the USB connector. However, due to issues with the board discussed in the testing section, this was not utilized. The sensor board was connected with USBA as the power draw from the sensors was minimal and USBA connectors were far cheaper than USBC. The sensor board would be communicated with utilizing I

2C. Also included on the
MCU board were 2 TPS54JA20 buck regulators, that would step the 12V line from the charge controller down to a usable 3.3V and 5V respectively. A comparator, A PTC fuse was utilized to ensure safe operation of the board and to reduce the likelihood of damage in the case of a short to ground. A comparator, Zener diodes, and LEDs were included as voltage indicators to simplify troubleshooting and to indicate whether the 3.3V and 5V lines were powered. A PTC fuse was utilized to ensure safe operation of the board and to reduce the likelihood of damage in the case of a short to ground. Throughout the board were jumper headers for various GPIOs, power lines and data lines, enabling easy troubleshooting. This proved invaluable during the testing process, as discussed in the testing section. Another revision of the MCU board was manufactured, to resolve some minor issues that occurred.
2) Servo Controller Board: The servo controller board was rather simple. A 5V LDO regulator would step down the 5V received from the USBC connector to the servo controller itself. The I²C data and clock lines were connected to the controller and pullup resistors. The 5V, GND, and the PWM line from the servo controller were connected to jumper headers for the servos to connect to.
3) Sensor Board: The sensor board was another rather simple board. This board featured five VEML7700 sensors, an 8-channel MUX and a USB connector. The 8-channel MUX was necessary because the VEML sensors come with the same I²C address by default, and this cannot be altered. To circumvent this, a TCA9548A 8-channel I²C MUX was used. This enabled us to address each sensor individually, by changing which line was open on the MUX before addressing the sensor. The USB-A connector delivered 3.3V, I²C data, clock and GND. The 5 sensors were placed on the board in a manner such that the sensor partition shown in Fig. 1 would be placed evenly between them. A switch was included on the sensor board to enable resetting the MUX during testing.
4) Stepper Controller Board: A stepper controller board was initially designed, however it proved faulty later. The first stepper controller board featured a controller that did not deliver enough current to drive the stepper, however functioned fine otherwise. The second revision of the board proved faulty, as discussed in the testing section. The second revision featured a USBC connector to connect to the MCU board and terminal connectors for testing. It was designed to operate on 12V from the charge controller and utilized a TB6560 as the controller. Optocouplers were utilized to isolate signals in conjunction with sensitive ICs, such as a CD74HC123 CMOS Multivibrators to ensure the stepper held its position when not actively stepping. The design was based on the devkit utilized but again, proved faulty.
V. SOFTWARE


Fig. 5. Overall software logic diagram.

### A. Ray Tracing Algorithm

The implementation of a solar tracking system involves precise adjustments of both horizontal and vertical components to effectively track the sun's position. The algorithm devised for horizontal tracking utilizes sensor data to dynamically adjust the stepper motor controlling the base of the tower. By analyzing sensor inputs and applying mathematical transformations, the algorithm ensures continuous and accurate movement of the base to maintain alignment with the sun's position. Similarly, the vertical adjustment of the mirror is achieved by correlating sensor servo movements and horizontal adjustments from stepper movements with the positioning of the mirror, adhering to Snell's law of reflection. Scaling operations are employed to translate sensor data using step sizes into precise vertical scaling in (3) and horizontal scaling in (4) for movements of the mirror, ensuring optimal reflection of sunlight towards the target:
vm =

(vs−495)(400−600)
765−495
+ 600, | (3)

ℎm =

ℎt(300−510)
1440
+ 510. | (4)

### B. Mesh Network Control

Incorporating the mesh network functionality through Zigbee communication protocols enhances the versatility of the solar tracking system. Leveraging the tower as a receiver allows real-time adjustment of the mirror's target position via signals transmitted through the mesh network. By storing target values in an array and toggling between them based on received signals, the system demonstrates seamless integration of multiple towers within the network. This integration facilitates efficient coordination and synchronization among different components, showcasing the system's adaptability and responsiveness to changing environmental conditions.

VI. TESTING

### A. Ray Tracing Algorithm

The functionality of various components for the project was tested to ensure proper operation. Firstly, the ESP32-C6 development boards were tested by powering them through USB-C ports and verifying GPIO pin voltages with a digital multimeter, as well as confirming reset button functionality. Similarly, the AdaFruit MicroSD card breakout board was tested by connecting it to the ESP32-C6 and inserting a microSD card, followed by readiness testing of the file system software. The hardware functionality of the VEML7700 light sensor was tested by wiring it to the ESP32-C6 and confirming proper connections, both physically and through software testing to ensure data transfer. The TCA9548A I2C Multiplexer underwent similar hardware testing, with connections to the microcontroller and sensors, ensuring proper data transfer through GPIO pins.
Additionally, the mechanical components were tested, including two servo motors attached for precise rotation of the reflector on the x and y axes, and another servo motor for vertical rotation based on sensor input. A stepper motor was used for the w axis, enabling rotation of the entire structure. Modifications to the ESP32-C6 development boards for antenna connections were noted, with possibilities for external antenna soldering. Simulations were conducted on the PCB designs, refining LED indicator circuits and voltage regulators through theoretical testing using tools like Fadstad circuits and TI Webench. Furthermore, the charge controller underwent testing powered by a DC power supply, addressing initial issues with over-voltage protection by configuring it specifically for LiFePo batteries. Real-world testing under load conditions is required to further validate its operation.

Similarly, the solar panel was tested outdoors, yielding the expected voltage output, but further testing under load conditions is necessary to ensure functionality in real-world scenarios.
During testing of the integration, there were multiple issues and errors encountered that were solved to effectively complete the project in a timely manner. Some of these issues were, but were not limited to, Inter-Integrated Circuit (I²C) rise times issues, faulty Zigbee coordinator equipment, issues pairing the ESP32-C6 to the Zigbee coordinator frontend, problems interfacing the multiplexer using software to control the sensors, and revisions to PCB design.
B. I

### 2C Issues

Some of the issues with I²C were due to higher than anticipated capacitance on the channel, resulting in slow rise time of signal pulses. These issues were resolved by reducing the clock rate of the I²C signal where possible, and where not possible, by reducing the resistance of pull-up resistors, whilst still considering the maximum current draw tolerable from the ESP32-C’s GPIO pins.


Fig. 6. | The I2C issue shown from an oscilloscope. The
low | frequency | signal | (shown | above) | shows | the
improvement in relative rise time over the high frequency signal (shown bottom).

### C. Mesh Networking Issues

The development of the mesh network faced a few major hurdles that had to be overcome. The first problem was a very rare issue with the first Zigbee coordinator dongle in which the UART bridge did not work, making it impossible to communicate with. This was understood by careful testing with an oscilloscope and a terminal attempting to send to the IC through the UART bridge. This was resolved by purchasing a new dongle.
The subsequent hurdles involved getting the hardware to work together. Using Zigbee2MQTT was a great help but also added challenges into the project. Getting the ESP32-C6 to pair with the coordinator hosted by Zigbee2MQTT was not a straightforward process but was eventually resolved by clearing cache on the microcontroller and working with the Zigbee2MQTT front end.
The other major issue was getting Zigbee2MQTT to see the microcontroller as a supported device. It is not an officially supported device since it can theoretically be coded to do anything. Due to this, it was required to check how the configuration files were set up for other similar devices so that it could be configured and interacted with properly.

### D. FreeRTOS Issues

Another issue faced was trying to read from multiple light sensors in a row using the I²C multiplexer using C code. Some of the issues faced while trying to create this using the ESP-IDF framework was that it was constantly going through software resets when reading from each sensor, due to issues from the FreeRTOS implementation that was used in previous example codes for similar products. It was ultimately decided to completely remove these libraries and code using them to create a custom channel select for the multiplexer to simplify the code.

### E. Voltage Sag Issues

Another challenge faced was the current draw from the servos causing a large drop in voltage on the servo boards 5V line. This would propagate down to the 3.3V line as the LDO regulator would not be able to operate below its dropout voltage. This would drop the enable pin on the servo controller below a logic 1, result in a brief inability to communicate to the servo controller, and a need to initialize the servo controller. In Fig.6 the issue can be seen visually. After some troubleshooting, the issue was determined to be cause by I

2R losses across a rather narrow trace, in addition to utilizing a lab power supply rather than the intended regulator. This resulted in the voltage sensing of the regulator being unable to maintain 5V at the distant servo controller board. This was resolved by using a conjunction of methods. The required current draw was reduced from the servo motors by reducing the instantaneous change in angle using software. The intended regulator was also installed, reducing the I²R losses and moving the voltage sense closer to the servo controller board. The combination of these changes resulted in this issue being resolved.


Fig. 7. The I²R losses visualized. In green is a measurement of voltage nearest the 5V regulator while the servos are running, and increasing in distance from the regulator are the orange and yellow respectively. The blue plot is the 3.3V I²C line. As can be seen the 3.3V line is impacted by the I²R losses on the 5V line due to the servos moving. The vertical discontinuities in the blue plot are the I

2C signals being sent.

### F. PCB Revision Issues

Some other design errors resulted in a desire to revise the initial MCU board. A mix-up between the TX and RX pins on the output of the USB/UART converter caused the device to detect the UART converter but not able to communicate to the ESP. In our first design the MCU board had the TX pin from the MCU connected to the TX pin of the UART converter and likewise for the RX pins. We were able to resolve this due to the prudent inclusion of jumper headers for the TX and RX pins, allowing us to use jumpers to bridge the pins. Another issue was a mix-up in the strapping pins. The GPIO pins that the ESP32-C6 uses for strapping pins differs between the Dev-kit and the standalone MCU. These differences resulted in the need to utilize jumpers to the strapping GPIO pins of the ESP, which was inelegant. This resulted in being unable to boot into the MCU. Again, the prudent inclusion of jumper headers for the GPIOs, enabled jumpers to be used to manually raise and lower the strapping pins, putting the ESP into and out of boot mode. The combination of these issues proved tedious and resulted in the desire to revise the board to solve these issues. The revision included a switch for to raise and lower the strapping pins to reduce time spent flashing code, enabling faster iterations of software, as well as fixing some other minor issues, such as the TX/RX mix-up and refining some footprints, silkscreen, and component placement.

### G. Stepper Issues

The initial stepper board worked, however only unloaded. Once the stepper had a load applied to it, the stepper would stall. This was due to the stepper controller being too small for the application. The second revision of the board featured a TB6560 controller. A development kit was tested under load and functioned fine, however after implementing a similar design on a PCB, the stepper motor had insufficient drawn in current when utilizing fabricated board. Only a tenth of the needed current was able to be drawn compared to development board. The issue is believed to be due to the current limiting resistors being of the wrong value, however this is untested. The group opted to utilize the development kit instead of troubleshooting the second iteration of the stepper controller board, to reduce costs of manufacturing another revision and reduce design time.

VII. CONCLUSION

In conclusion, ASTROCOM project demonstrated the solar reflector system and mesh network functions as expected and meets specified requirements. The power output of the system is sustainable for an extensive period of use. The reflection angles ranges are wide enough to have a large area of coverage. However, there exist many opportunities for improvement through the integration of photonics’ and mechanicals’ expertise. Enhancements such as improved rotation mechanisms, advanced materials for reflecting sunlight, and optimized solar reflector algorithms can significantly enhance the system's performance. Furthermore, by scaling up in term of funding and placing the materials to meet constrained environments, notable improvements can be achieved. For instance, utilizing gold alloy for mirror construction, or employing aluminum and mylar coatings instead of plastic and adhesive for mirror manufacturing. Parts’ housing can incorporate carbon fiber to enhance both efficiency, weight, and durability. Additionally, protective measure can implement by insulation to the computer board. Transitioning to industrial servos capable of withstanding high heat fluctuations is essential for ensuring reliable operation in challenging conditions.
Mesh network can be expanded be integrating router nodes throughout the network architecture. Additional Zigbee commands can be implemented to increase the network’s functionality. Image’s packages can be move through the network and temporary stored in the implemented storage of the designed board.
In summary, while the current solar reflector system
meets | basic | requirements, | ongoing | research | and
development efforts focused on integrating advanced technologies and materials will be instrumental in optimizing its performance and expanding its potential applications.

ACKNOWLEDGEMENT

The authors would like to acknowledge the support of Chan Chung Yong, PhD and Arthur Weeks, PhD first and foremost for their unrelenting support and mentoring throughout the project’s planning and implementation. Also deserving of recognition is the Florida Space Institute as the project’s sponsor with Mr. Mike Conroy as the main agent providing funding and support for the project as well as keeping track of the project’s progress, objectives and goals.
The University of Central Florida has graciously provided the excellent facilities that allowed for efficient work on the project such as the Senior Design Lab, Junior Design Lab and the Texas Instruments Innovation Lab. Last but not least, a thanks to the reviewers that agreed to be on our project’s committee: Mike Borowczak, PhD, Mingjie Lin, PhD, and Saleem Sahawneh, PhD.

BIOGRAPHY

Alexandre Fiset is a senior in Electrical Engineering at UCF set to graduate in May 2024. He has previous experience working as a student intern at the Orlando Utilities Commission and is currently engaging in undergraduate research in DER Cybersecurity with the RISES Center at UCF. He plans to continue his education, seeking a master’s degree in electrical engineering from UCF.
Pedro Kasprzykowski is a senior in
Computer | Engineering,
Comprehensive Track at the University of Central Florida set to graduate in May 2024. He will be starting a PhD in Computer Science at the University of Colorado Boulder in August 2024. His long-term goal is a career in teaching as a university faculty member.

Stephen Martin is a current senior set to graduate in May 2024 with a bachelor’s degree in Computer Engineering,
Comprehensive | Track | from | the
University of Central Florida (UCF). He plans to pursue graduate school at
UCF | studying | Engineering
Management while remaining a member of the UCF football team.

Binh Pham is a senior Computer Engineer student in VLSI track at the University of Central Florida. He will finish his undergraduate studiesin May 2024 and continue to pursue a master’s degree in the same field and graduate in May 2025. His career goal is to incorporate Engineer and Chemistry in biomedical industry.

REFERENCES

[1] “ESP | DevKits | | | Espressif | Systems,”
www.espressif.com. | https://www.espressif.com/en/
products/devkits/esp32-devkitc. (accessed Nov. 24, 2023).
[2] “Power | Designer,” | webench.ti.com.
https://webench.ti.com/power-designer/switching-regulator/customize/5 (accessed Dec. 04, 2023).
[3] “Renogy | RNG-50D-SS.” | [Online]. | Available:
https://www.renogy.com/content/RNG-50D-SS/RNG-50D-SS%20G2%20Datasheet.pdf
[4] “Vishay Semiconductors High Accuracy Ambient Light Sensor With I 2 C Interface Pinning,” Apr. 2022. Available: https://www.vishay.com/docs/84286/veml7700.pdf
[5] “‘Step Motor – Basic Structure & Operation.’ Moving
In | Better | Ways!,” | www.moonsindustries.com.
https://www.moonsindustries.com/article/basic-structure-and-operating-principle-of-stepper-motor (accessed Dec. 04, 2023).
[6] “ZigBee | Specification | FAQ,” | web.archive.org.
https://web.archive.org/web/20130627172453/www.zigbee.org/Specifications/ZigBee/FAQ.aspx (accessed Nov. 24, 2023).
[7] A. Sánchez-González and J. Yellowhair, “Reflections between heliostats: Model to detect alignment errors,” Solar Energy, vol. 201, pp. 373–386, May 2020, doi: https://doi.org/10.1016/j.solener.2020.03.005.
[8] robmilne.ca, and Instructables, “Heliostat Offset Mirror
Algorithm,” | Instructables, | Dec. | 06, | 2021.
https://www.instructables.com/Heliostat-Offset-Mirror-Algorithm

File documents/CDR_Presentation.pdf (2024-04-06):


A.S.T.R.O.COM.

ADVANCED SOLAR TRACKING AND ROVER OBSERVATION COMMUNICATION

Alex Fiset | Pedro Kasprzykowski | Stephen Martin | Binh Pham
Electrical Engineering | Computer Engineering | Computer Engineering | Computer Engineering

## MOTIVATION AND BACKGROUND

- South Pole of Moon is area of interest for researchers
- Lunar south pole has many craters that are in permanent darkness due to the sun's path across the lunar south pole's sky
- Approached by FSI to solve a few problems for lunar exploration:
1. Permanently dark locations on the moon are difficult to explore
- Lack of power infrastructure on the moon limits exploration
- Permanently dark locations are a valuable location for research
2. Communication on lunar surface is limited
- Range of communication limits exploration of craters
- Limited communication infrastructure on moon

## MOTIVATION AND BACKGROUND

- Proposed Solution:
1. A heliostat tower
- To reflect light from the sun into permanently dark locations
- Equipped with communication capabilities
2. A smaller communication beacon
- Carriable by rovers
- Form a communication network with rovers

## GOALS

Overall Goals (High Level)

- Build a tower to handle rover communication.
- Build a tower to handle sunlight diversion to targets.

Stretch Goals

- P2P Networking for communication and mirror tower with rovers.
- Wireless charging and/or docking station for communication tower.

## OBJECTIVES

Mirror Tower Objectives (Lower Level)

- Identify optimal sun location based on lux value from sensor.
- Receive requests from communication tower using protocols.
- Create a heliostat algorithm to orient towards the target with motors.
- Create a self-sustainable power supply using solar and battery power.

Communication Beacon Objectives (Lower Level)

- Receive requests from target through mesh network protocols.
- Relay requests to mirror tower using communication protocols.
- Create a small and portable tower that can be moved by rovers.

Heliostat Tower
Minimum Temperature | -40°C
Reflector
Minimum size | 1ft diameter
Maximum size | 5ft diameter
Maximum Weight | 9kgs
Minimum Reflectivity | 90%
Response Time | 3 minutes
Tower Frame
Maximum total weight | 27kgs
Minimum Weight Capacity | 10kgs
Solar Panel
Minimum Power | 30W during | sunlight hours
Maximum Voltage | 24V
Battery
Minimum Lifespan | 2 weeks without sun

Communication Tower
Minimum Enclosure Volume | 6.5"x6.5"x5"
MaximumWeight | 2kg
Minimum Network Range | 20m
Communication Rate | 2400MHz
Voltage input | 3.3V or 5V
Maximum Current Draw | 500mA
MinimumTemperature | -40°C
Latency | 1 second
Maximum | Power | 5W

## SPECIFICATIONS TABLE


H A R DWA R E
B L O C K
D I AG R A M


SOFTWARE
BLOCK
DIAGRAM

## COMPARISON AND SELECTION OF HARDWARE

- MCU
- Solar Panels
- Voltage Regulation
- 3Charge Controller
- Reflectors
- Motors
- Motor Controllers
- Sensor
- Batteries
- Antenna

MCU

Criteria | Microcontroller | FPGA
Environmental robustness | ✓
Low power consumption | ✓
Parallel processing | | ✓
Ease of use | ✓
Processing power | | ✓
Cost | ✓
Scalability | | ✓
Integration/Peripherals | ✓
Documentation | ✓
| ESP32 | MSP430 | Raspberry Pi 0 | Arduino MKR1310 | Arduino MK1010
Cost -Processor & DevKit (USD) | 9.18 | 20 | 15 | 46 | 38.6
Wi-Fi | Yes | No | Yes | No | Yes
Bluetooth | Yes | No | Yes | No | Yes
Zigbee | Yes | No | Yes | No | No
Z-Wave | No | No | Yes | No | No
LoRaWAN | No | No | Yes | Yes | No
6LoWPAN | No | No | Yes | No | No
UART | Yes | Yes | Yes | Yes | Yes
I2C | Yes | Yes | Yes | Yes | Yes
SPI | Yes | Yes | Yes | Yes | Yes
PWM | Yes | Yes | Yes | Yes | Yes
ADC | Yes | Yes | Yes | Yes | Yes
DAC | Yes | Yes | No | Yes | Yes
Flash Memory | 4 MB | 128 KB | None | 256 KB | 256 KB
RAM | 520 KB | 2 KB | 512 MB | 32 KB | 32 KB
Operating Voltage (V) | 3.6 | 5 | 5 | 3.3 | 3.3

Current Draw
(A) | 0.379 | 0.2 | 2.5 | 0.154 | 0.154
Power
Consumption
(W) | 1.3644 | 1 | 12.5 | 0.5082 | 0.5082
- Microcontroller was chosen over FPGA, presenting characteristics that were better fits for the project such as low power consumption, cost and high amounts of documentation.
- ESP32 had the best combination of low cost, low power and networking capabilities and all connections required.

SOLAR PANELS

Solar Panel Technology | Efficiency | Low-Light Perf. | Temp. Tolerance | Radiation Resistance | Degradation | Weight & Size
Monocrystalline | High | Excellent | Good | Good | Low | Relatively heavier
Polycrystalline | Moderate | Good | Good | Good | Low to Moderate | Moderate
Thin-Film | Low | Varies | Good | Varies | Moderate to High | Lightweight & Flexible

SOLAR PANELS

Model | RNG-50D-SS | HQST-50P-US | SP-52-L
Brand | Renogy | HQST | Solbian
Technology | Monocrystalline | Polycrystalline | Monocrystalline
Price | $ 59.99 | $ 65.99 | $ 499.00
Pmax at STC | 50 W | 50 W | 52 W
Voc | 22.3V | 23.3V | 10.9V
Vmp | 18.6V | 19.8V | 9.1V
Imp | 2.69A | 2.53A | 5.7A
Isc | 2.94A | 2.63A | 6A
Weight | 7.7 lbs | 8.4lbs | 1.8lbs
Dimensions (inches) | 22.9 x 20 x 1.2 | 25.9 x 18.6 x 1.2 | 43.7 x 11.49 x 0.1
Temp Coefficient of Pmax (%/degC) | -0.37 | -0.37 | -0.38

VOLTAGE REGULATION

Specifications | Linear Regulators | Switching Regulators
| | Buck | Boost | Buck-Boost
Efficiency | Moderate | High
Heat | Moderate | Low
Voltage Output | Step-Down | Step-Down | Step-Up | Up or Down
Output Ripple | Low | Low | High | Low
Complexity | Low | Moderate | Moderate | High
Cost | Low | Moderate | Moderate | High

VOLTAGE REGULATION

Model | LM1085IT-5.0/NOPB | DROK MiniBuck Converter | LM2596 | TPS54JA20
Brand | Texas Instruments | DROK | Texas Instruments | Texas Instruments
Input Voltage | 2.6-26V | 2.5-24V | 3-40V | 2.7–16V
Output Voltage | 3.3 or 5 | 3.3 or 5 | 1.5 to 35 | 0.5 to 5.5V
Output Current | 3A | 3A | 3A | 12A
Price | 2.19 | 1.97 | 1.495 | 0.65
Type | LDO Buck | Buck | Buck | Buck

CHARGE CONTROLLER

- Two broad categories of Solar Charge Controllers:
1. PWM
- Basic pulse width modulation
- Lower efficiency
- Cheaper
2. MPPT
- Tracks highest power producing operating point
- Higher efficiency
- Typically, more expensive

CHARGE CONTROLLER

Model | BQ25798RQMR | SR11004 | Adventurer
Brand | Texas Instruments | SMARAAD | Renogy
Input Voltage | 24V max | 26V max | 50V max
Output Voltage | 18.8V max, Programmable | 12/24V | 12/24V
Output Current | 5A | 10A | 30A
Price | 6.25 | 39.99 | 59.99
Power | Not Specified | 260W | 1500W
Type | MPPT | MPPT | PWM
Programming MPPT | I2C | Not Specified | NA
MPPT Type | Sets Voltage to % of Voc | Not Specified | NA
Charge controls | Programmable | Battery Chemistry presets | Preprogrammed depending on chemistry

REFLECTORS

- Material Chosen to fabricate:
- Aluminum has high heat resistance, durable, and high reflectivity in the moon environment.
- Mylar increase reflectivity instead of glass which has higher heat change resistance and won’t crack, which reduces quality of refection
- Proof of concept: plywood as cheaper alternative and easier to fabricate.

MOTORS

- Stepper motor: Nema 34 robustness and strong torque to control the rotation of the whole tower. Can be used on DC system
- Incorporated gearbox to increase movement range and control for stepper motor.
- Servo Motors: a cheaper alternative for smaller part movements.


Types of Motors | DC Brush | DC Brushles s | AC | Stepper | Servo
Financial Cost | Small: $5-$50 Medium: $20-$100 | Small: $10-$100 Medium: $100-$500 | Small: $50- $200 Medium: $200-$2,000 | Small: $10-$50 Medium: $50-$200 | Small: $50-$200 Medium: $200-$1000
Size | ~8mm-35mm | ~13mm-35cm | ~10cm-30cm | ~0.4cm-20cm | ~0.4cm-10cm
Torque | 0.36-160 nNm | 4-400 nNm | 203000Ncm-610000Ncm | 10-10000Nc m | 10-1000Ncm
Speed | 5,000 to 14,000 rpm | 100,000 rpm | 1800-3600 rmp | Low | High
Voltages requireme nt | 4.5V/4.5V/7.0V | 4-24V | 115V/208V/230V | 3V-100V | 3V-100V
Durability | High | High | High | High | Low
Weight | 0.5-160g | 10-1000g | 750g | 150-5000g

MOTOR CONTROLLERS


- Stepper Controller DRV8834, cheap and can handle the amperage provided by the system.
- PCA9685 PWM: Design specific for servo and can control all three servos planned in the system, compatible with ESP32 C6 and run on I2C protocol.

BATTERIES

Specifications | Lead Acid | NiCd | NiMH | Li-ion
| | | | Cobalt | Manganese | Phosphate
Specific Energy | 30-50 | 45-60 | 60-120 | 150-250 | 100-150 | 90-120
Internal Resistance | Very low | Very low | Low | Moderate | Low | Very low
Cycle Life | 200-300 | 1000 | 300-500 | 500-1000 | 500-1000 | 1000-2000
Self-Discharge/month at RT | 5% | 20% | 30% | < 8%
Operating Temperatures | -20 to 50 C | 0 to 45 C | 0 to 45 C | 0 to 45 C
Maintenance Requirements | 3-6 Months topping charge | Full discharge every 90 days | | Maintenance free
Safety Requirements | Thermally stable | Thermal stable, fuse protection | | Protection circuit mandatory
Cost | Low | Moderate | | High

BATTERIES

Model | ML5-12 | HW-4F7 | PQ12V/6AH
Brand | Mighty Max Battery | Howell Energy | Power Queen
Voltage | 12 | 12 | 12.8V
Amp Hour | 5 | 7 | 6
Technology | SLA AGM | LiFePO4 | LiFePO4
Price | 16.99 | 32.99 | 19.59
Temperature Rating | -20 to 50 | -20 to 70 | Not Specified
Weight | 3lbs | 1.9lbs | 1.8lbs
Dimensions | 3.5 x 2.8 x 4.2 | 5.9 x 2.6 x 3.7 | 5.9 x 2.6 x 3.7
Charging Requirements | CV | CC 3.5A, CV 14.6V, Built-in BMS | Not Specified, Built in BMS

SENSOR

| VL6180X | MAX44009 | SI1145 | VEML7700
Cost (USD) | $14.49 | $5.96 | $9.95 | $4.95
Measuring Principle | TOF/IR Laser Photodiode | Photodiode | IR-LED Photodiode | Photodiode
Max Lux | 100000 | 188000 | 128000 | 120000
Ambient Light Sensing | Yes | Yes | Yes | Yes
IR Sensing | No | No | Yes | No
UV Sensing | No | No | Yes (extrapolated) | No
Operating Voltage (V) | 3 | 3.6 | 3.6 | 3.6
Operating Current (mA) | 0.3 | 0.0003 | 7 | 0.0045
I2C | Yes | Yes | Yes | Yes
SMBus | No | Yes | No | No
ADC | Yes | Yes | Yes | Yes
Size (mm^2) | 234 | 4 | 360 | 15.98
Operating Temperature ( C ) | [-20 - 70] | [-40 - 85] | [-40 - 85] | [-25 – 85]
C/C++ Libraries | Yes | Yes | Yes | Yes

Sensor Final 4 Options:

- VL6180X and SI1145 include IR which is not needed
- MAX44009 only has breakout board; does not work for PCB
- VEML7700 best choice for price/ability

## COMPARISON AND SELECTION OF SOFTWARE

- Vectoring and Positioning / Solar Tracking Algorithm
- Communication technologies
- Development Environment: Languages and Repositories

DEVELOPMENT ENVIRONMENT: LANGUAGES AND REPOSITORIES

Programming Languages
- C: best choice for MCU programming, low-level
- Java: best for object-oriented programming, low-level
- Python: best for existing libraries, high-level

Choice: C

Repositories
- GitHub: most popular repo, widely used among many software devs
- Bitbucket: Git based repo, includes task scheduling and team goal software

Choice: GitHub

VECTORING AND POSITIONING / SOLAR TRACKING ALGORITHM

Algorithms | Heliostat | Kalman Filtering | Skyview Factor | Ray Tracing | Two-axis Solar Tracking System | Sun tracking Photodiode
Financial Cost | Open Source | Ambiguous | Open Source | Not available | Open Source | No available
Sensor | Ambient Light | Ambient Light | Ambient Light | Ambient Light | Ambient Light | Photodiode
Algorithm code library | Available on GitHub | Available in python | Available on GitHub | Available in Research paper | Available in GitHub | Not available
Efficiency | High | Low | Medium | Medium | High | High
MCU compatibility | Good (C Language) | Fair (Python) | Bad (R Script) | Good (C Language) | Good (C Language) | Bad (No code)
Additional Requirements | Change to an algorithm to change light measuring location | Compass Reading or gyroscopic data

ANTENNA

| Dipole | Patch | Reflector (Parabolic) | Yagi – Uda | Helical Antenna | Aperture (Horn)
Gain (dBi) | 1.76-7 | 0.5 -10 | 10 - 40 | 5 – 20 | 3 – 15 | 10 – 25
Polarization | Linear | Linear/ Circular | Circular | Linear | Circular | Linear/ Circular
Efficiency | High | High | High | High | High | Very High
Bandwidth | Narrowband | Wideband | Narrowband | Narrowband | Wideband | Narrowband
Directivity | Omni -directional | Omni - directional | Highly Directional | Highly Directional | Directional | Highly Directional
| PC140 | WPC.25A | FXP74 | PC17 | FXP70
Average Gain (dB) | -1.92 | -1.14 | -2 | -3.6 | -2
Peak Gain (dBi) | 1.67 | 5.15 | 4 | .9 | 1.1
Efficiency (%) | 64 | 76.9 | 50 | 44 | 63.7
VSWR | <2 | <2 | <2 | <1.5 | <1.5
Polarization | RHCP | Linear | Linear | Linear | Linear
Cost (USD) | $27.26 | $9.21 | $7.69 | $16.60 | $27.09
- The combination of the certain gain range, circular polarization, high-efficiency and wideband characteristics made patch and helical antenna types the ideal choices.
- The PC140’s circular polarization while also being above average in gain and efficiency made it the preferred antenna product.

COMMUNICATION TECHNOLOGIES

Criteria | Wi-Fi | LoRaWAN | Bluetooth | 6LoWPAN | Zigbee | Z-Wave
Range (m) | 45 | 15000 | 10 | 100 | 980 | 800
Data rate | 54 Mbps | 50 Kbps | 1 Mbps | 250 Kbps | 250 Kbps | 100 Kbps
Power consumptio n | 30 uA-250 mA | 1 uA-16 mA | 9 uA-39 mA | 0.3 uA-35 mA | 12 uA- 54 mA | 1 uA-23 mA
Max devices | 255 | 120 | 3-4 | 100 | 100 | 232
Scalability | ✓ | ✓ | | ✓ | ✓ | ✓
Frequency | 2.4/5/6 GHz | 902.3-914.9 MHz | 2.4 GHz | 2.4 GHz | 915 MHz/2.4 GHz | 908-916 MHz
- The combination of low power consumption, suitable range, options for frequency and high scalability made Zigbee the ideal
communication technology to implement.


## HARDWARE DESIGN


- Design two separate towers, each with their own design constraints
- Majority of focus is on heliostat tower, as it is more complex
- Schematics and PCB designs
- Heliostat structure
- Tripod on a "Lazy Susan"
- Communication Beacon
- Antenna on an enclosure


POWER DELIVERY/ ELECTRICAL POWER SYSTEM


STEPPER MOTOR CONTROLS


SERVO MOTOR CONTROLS

## SENSOR CONTROL


## MCU SYSTEM


## LOWER-LEVEL SUBSYSTEM



## SOFTWARE DESIGN

- Details on software design for the overall system which includes:
- Communications through the mesh network
- Collecting sensor information
- Positioning reflector to deliver sunlight to target
- Represented with software diagrams


CASE
DIAGRAM


ACTIVITY
DIAGRAM


MOTOR POSIT IONING
OF REFLECTOR B ASED
ON LIG HT INT E NSITY
ALG OR IT HM.


MOTOR POSIT IONING
OF REFLECTOR B ASED
ON LIG HT INT E NSITY
ALG OR IT HM

POWER CONTROL ALGORITHM

Component | Essential/Non-Essential | Low-Power Considerations
MCU | Essential | Low-Power Mode, only essential functions
Antenna | Essential | Receive only
Sensors | Essential | Sensors will be turned on periodically
Stepper Motor | Non-Essential
Servo Motors | Non-Essential
- Goal was to reduce power consumption when the sun would not be visible
- Reducing usage of non-essential components during these times would preserve battery charge


## PCB DESIGN

- MCU
- Sensors
- Stepper Motor Controller
- Servo Motor Controller


# MCU PCB


# SENSORS PCB


STEPPER MOTOR
CONTROLLER PCB


SERVO MOTOR
CONTROLLER PCB

## ADMINISTRATIVE CONTENTS

Electrical Engineering | Responsibilities
Alexandre Fiset | PSU Design and Implementation
PCB Design
MPPT Tracking Implementation Administrative Documentation
Computer Engineering | Responsibilities
Binh Pham | Reflector Technology and Design
Motor and Motor Controls
Vectoring Technology
Project Lead
Positioning and Vectoring Algorithm
Computer Engineering | Responsibilities
Pedro Kasprzykowski | MCU Selection and Implementation
Software Design and Implementation Antenna and Communications Website Design and Management
Computer Engineering | Responsibilities
Stephen Martin | Sensor Selection and Implementation
MCU Selection and Implementation Positioning and Vectoring Algorithm Software Design and Implementation

Distribution of work table

## MECHANICAL'S BUDGETS

Component | Name | Price/unit | Quantity
Mirror | 0.032" x 24" x 24", 3003-
| H14 Aluminum Sheet | $28.86 | 1
Mirror Coating | Mylar Sheet | $25.99 | 1
Frame | ADJ LTS-6 T-Bar Tripod
| Lightweight Lighting Stand | $54.99 | 1
Base Panels | Plywood Panels 4ftx8ft | $25.60 | 2
Communicatio n Tower Box | Junction Box | $26.89 | 1
Wheel Hub Bearing | Rear Wheel Hub | $44.90 | 1

## ELECTRICAL’S BUDGET

Component | Name | Price | Quantity
Battery | Howell Energy hw- 4f7 | 32.99 | 1
Motor w | Nema 23 | $30.73 | 1
Motor x-y-z | 9.5-11kg*cm Servo Motor | $17.59 | 3

Charge
Controller/BMS
Smaraad SR11004 | $39.99 | 1
Solar Panel | RNG-50D-SS | $49.99 | 1
Microcontroller | ESP32-C6-DEVKITC- 1-N8 | $9.00 | 1
External Antenna | Wlaniot 2.4G | $17.98 | 2
MicroSD card | 5251 | $4.50 | 2
MicroSD card breakout board+ | 254 | $7.50 | 1

## PCB’S BUDGET

Component | Name | Price | Quantity
Microcontroller for PCB | ESP32-C6-WROOM-1U | $3.48 | 1
Stepper Motor Controller | DRV8833PW | $2.84 | 1
Servos Motor Controller | PCA9685PW,112 | $2.64 | 1
3.3V Regulator | TPS54JA20 | $1.50 | 1
5V Regulator | TPS54JA20 | $1.50 | 1
USB-A Connector | 2057-USB-AP-S-RA-SMT-ND | $0.55 | 3
Sensor-MUX | TCA9548APWR | $1.78 | 1
Sensor | VEML7700 | $1.88 | 5
USB-to-UART Bridge Controller | CP2102N-A02-GQFN28 | $4.07 | 1
MicroSD Socket | 1660 | $1.95 | 1
Misc. | Resistors, Capacitors, Inductr,
| Jumpers, Etc.…. | ~$20.00

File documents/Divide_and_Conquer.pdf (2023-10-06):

A.S.T.R.O.COM.

## Advanced Solar Tracking and Rover Observation Communication

Authors:

Alex Fiset Pedro Kasprzykowski | Stephen Martin | Binh Pham
Electrical | Computer | Computer | Computer
Engineering | Engineering | Engineering | Engineering

Reviewer Committee:

Dr. Mike Borowczak | ECE | Associate Professor
Dr. Mingjie Lin | ECE | Associate Professor
Dr. Saleem Sahawneh | ECE | Lecturer
Mike Conroy | FSI | Sponsor/Engineering Support

Mentor:

### Dr. Chung Yong Chan


## Chapter 2-Project Description

## 2.1 Project Background and Motivation

In the vast expanse of space exploration, where humanity's curiosity knows no bounds, our senior design project endeavors to tackle the intricate challenges surrounding rover communication systems and heliostat light reflection. As we venture into uncharted territories, we confront the fundamental hurdle of establishing robust and reliable communication networks between rovers and their human counterparts, bridging the vast distances that separate us. Simultaneously, we grapple with the complexities of harnessing the power of heliostat light reflection, leveraging this innovative technology to illuminate unexplored regions and unravel the mysteries hidden within. With unwavering determination and pioneering spirit, our project aims to revolutionize the way we explore and educate others, pushing the boundaries of engineering and innovation to forge a path towards the stars.

In our academia, the senior design project is a great way for undergraduate students to learn to work in teams to achieve a common goal. As a group, we must learn to overcome challenges to brainstorm, innovate, and design a functional project with multiple pieces of software and hardware. Using these factors, we decided that we wanted to pick a project that would not only challenge us but also motivate and inspire us to make change. Because of this, we decided that we wanted to think big for our project.

Our group was approached by a sponsor, Mike Conroy from Florida Space Institute (FSI) Student Design Projects. Mike is a well-respected mentor who has over 35 years of experience working with the National Aeronautics and Space Administration (NASA) as an engineer, team leader, and now senior design mentor. We knew we had an unbelievable opportunity to have a great mentor and idea for a project. A recommendation from our sponsor resulted in a project idea as we were brainstorming different topics and ideas to build an engaging and challenging senior design project. This recommendation was a project to build a mesh communication network with a set of rovers through a main communication tower along with a reflection system to give these rovers light when they might possibly be in a shadow behind a hill.

## 2.2 Current Commercial Technologies and Existing Projects

### 2.2.1 Heliostaat DIY Kit

The Heliostaat DIY kit is a commercially available product that uses a mirror to reflect sunlight at a specified location at all times. It does not use any light sensors to achieve this result. It uses a combination of GPS and calculations to determine its positioning. It uses two motors to move the mirror into position. The system is made to last for years even in the event of power failure. The Heliostaat can operate in two modes. The first mode of the product is to be a lamp that is on all day while reducing waste and space from a conventional lamp. The other mode is tracking the sun to maximize output for a solar panel.

The Heliostaat is meant to be low power and is controlled by a remote control. It uses a 12/24 V adapter to power and averages 430 mW. The remote control operates at 433 MHz with a maximum range of 50 meters when in an open area. It is unspecified what motors are used in the product but they are normally used for dish antennas. The software and hardware are both highly accurate with

0.01 degrees of accuracy for the software and 0.0125 degrees for the hardware. The internal processor runs at 48 MHz and the system has an LCD display with information on date, time and positioning on it. It’s possible to modify the firmware if desired as well as use your own motors and add a wind sensor.

Heliostaat shares many similarities and differences with ASTROSCOPE. Both projects seek to track the sun and reflect sunlight using motors as the main idea. Both projects are controlled in some form with a remote control. The biggest differences lie within the use cases and how that end result will be achieved. For ASTROSCOPE the possibility using GPS does not exist as it will be used on the moon. This is the largest difference between the method of the two as ASTROSCOPE will require light sensors, Heliostaat does not. Both, naturally, will need to use calculations to determine any positioning but ASTROSCOPE cannot take can any action without the light sensors.

Another difference is the reliance on a mesh network hosted by a communications tower so that information can be transmitted between the reflector and one or more rovers that need light reflected to their location. Heliostaat doesn’t handle changing positions on demand for moving objects. It does calculations by knowing its own position through GPS and everything else falls into place as that will reveal where the sun rises and where the sun sets for every day of the year. For ASTROSCOPE all positioning calculations are reliant on information being sent through the mesh network so that such calculations can be performed and light can be reflected to the given rover.

Overall, the very similar core ideas show that Heliostaat is one of the most similar products on the market to ASTROSCOPE. That said, it is only the reflector tower part of the project and doesn’t involve anything to do with the moon or rovers. The integration of a scalable mesh network with a movable communications tower to coordinate sunlight positioning makes ASTROSCOPE more complex and wider in scope.

### 2.2.2 FSI Rover and App


Figure 2.1. FSI Rover and App from previous project.

This was a congregation of previous projects that have been built for multiple years and universities, and we would be next in line to improve the rover project. Other schools had built this rover to be fully operational and able to be remotely operated through an app using Raspberry Pi Wi-Fi. Although the rover had been significantly upgraded, the communication aspect and the electrical components of the rover were lacking. This was a unique challenge for us to be the next group to take the rover project to the next step.

We decided to take this challenge head on. At the time, the group that was constructed had eight people total and we decided to split the groups into a “rover group” and a “tower group” to effectively break this project up into two senior design projects that coincide together. We picked our groups that gave us the best chance to build two successful projects that would work together using the advice and guidance from our mentor professor, Dr. Chan. We brainstormed ideas of the functionalities early on and got a head start on our project, beginning planning and constructing diagrams as early as Spring 2023.

For this project, the main goal of this would be an education source for elementary and middle school kids and a proof of concept to a company such as NASA that they could build off, rather than something that would be put on the moon. FSI would supply us with a budget that would allow little to no cost for this project if we stayed within the boundary of $750.00. This gave us an unbelievable opportunity to build an interesting senior design project that would be fully funded by a sponsor company while also being a contribution to children’s education in space exploration and communication systems.

As we started brainstorming how we wanted to attack this project, we did not think it would be feasible to have both communication and light reflection on the same tower since it would be too heavy and hard to balance the power draw from the microcontroller. We decided it would be best to break up the communication and mirror reflection into two separate towers to ease the power draw and make it simpler to divide the work among our group. The first tower, which will be the bulkier tower because of the motors and large mirror to reflect light to the rovers, is the “mirror tower”. The other tower is the “communication tower”, which will be light and compact, and theoretically can be picked up by the rover and placed somewhere else.

From here we started picking team roles and areas we wanted to work with based on undergraduate majors and personal preferences. We have three computer engineers in our group and one electrical engineer, so we based our roles mostly on these parameters. Binh was selected to be the project manager and to be in charge of the motors and mirror reflection. He is a computer engineer studying the Digital VLSI Circuits track at UCF which focuses on hardware-software co-design, making him the right person for the job. Alex, the electrical engineer, would oversee the power supply unit (PSU) in both the mirror and communication tower for the project, as he has the most experience with this field. Rounding up the group working on the mirror tower is Stephen, who is managing the microcontroller and light sensing algorithm for the mirror tower. He is a computer engineer so creating this algorithm relies heavily on coding and computer science resources to do this. Lastly, the person captaining the communication tower is Pedro, who is the last computer engineer of the group, and will be using network protocols and computer science algorithms to create the mesh network communication system with the rovers through the antenna. From here, we started working on our research and project specifications that will be laid out in this project report.

As our main motivation for this project, it is to complete the senior design program, which serves as the capstone program for the College of Engineering and Computer Science at UCF, and to meet the needs of our sponsor, FSI, as they will be the ones funding the project. As we meet these necessary requirements, there are some internal motivations as well. Each group member wants to use this project as an opportunity to complete a team project with different roles to achieve a common goal, which will be incredibly prevalent as we enter the workforce in the industry after our graduation. On top of this being a great resume booster for any job application, this project will allow us to build necessary skills that will be used in the industry in the real world. These factors will be extremely important for early success by using these skills will allow us to make good first impressions and move up quickly with our respective companies.

Another piece of motivation for this project is to use this as a great opportunity to build a project full of innovative hardware and software to help with education for elementary and middle school students to teach and inspire them to learn about math and science to be the engineers of the future. On top of this, this could be an inspiration for an organization such as NASA to build upon this to create a more advanced system that could be used for future space exploration. This extra motivation keeps our group motivated, on pace, and thinking outside the box to inspire a future generation.

### 2.2.3 Summary

Overall, looking into currently available commercial technologies and past projects that relate to our current product gives a lot of insight into where we can take this project, how we can match what exists and build upon it in a new direction. Not only that but learning about real existing solutions that are related helps with setting down constraints and understanding practical requirements that must be met for a successful project.

In the special case of our sponsored project, we are actively building upon FSI’s rovers with new ideas that will work with them. It’s integral to our new project to understand the constraints placed on the rover’s design off the bat. Our main concerns are the addition of a reflector tower and a communications tower that are both integrated with the rover through a mesh network.

The reflector tower is completely separate from the rover and the communications tower aside from their communication through the network. The communications tower needs to be small and light enough so that it could potentially be transported by the rover. The rover must also be modified to be able to communicate with our network design.

By looking at the DIY Heliostaat kit, there was a lot to learn about creating an effective reflector. While the context was completely different, locating the sun and reflecting its light to a given point is how both our project seeks to function and how Heliostaat functions. It evidenced how we could not use GPS when we are on the moon and must rely on sensors to get the desired result.

The commercially available kit also showcases price points that we would hope to match or go lower in comparison. Budgeting from our sponsor is a major concern for our project and having an idea of the cost for something similar helps to gauge expectations and goals, as well as understanding what parts are more expensive or what parts deserve more budget allocation.

In conclusion, this less formal and less technical part of researching for the project was important for many reasons. Seeing currently available and past complete projects affects where we want to take our decision making and goals. Special attention goes to the FSI rovers as they are an integral part of our intended complete system within our project.

## 2.3 Objective and Goals

The main idea of this project is to build a communication tower and mirror tower to supply the rovers with a mesh communication network and sunlight for solar charging. Some of the main goals and objectives are listed below.

Overall Goals

- Build a tower to handle rover communication.
- Build a tower to handle sunlight diversion to rovers.

These goals can be narrowed into the objectives of both the mirror and communication tower to successfully create the project.

Mirror Tower Objectives

- Identify optimal sun location based on lux value from sensor.
- Receive requests from communication tower using protocols.
- Create a heliostat algorithm to orient towards the target with motors.
- Create a self-sustainable power supply using solar and battery power.

Communication Tower Objectives

- Receive requests from rovers through mesh network protocols.
- Relay requests to mirror tower using communication protocols.
- Create a small and portable tower that can be moved by rovers.

Stretch Goals

- Peer to Peer Networking for communication and mirror tower with rovers.
- Wireless charging and/or docking station for communication tower.

### 2.3.1 Hardware

### 2.3.1.1 Reflector – Basic Goal:

The ASTROSCOPE’s reflector tower’s primary function is to redirect sunlight to a specific location as rovers or facilities requested when the elements are obstructed by shadow. The facilities use redirected sunlight as replacement energy directly from the sun. The reflector needs to be able to traverse through the range of the sun’s path and find the highest amount of sunlight possible to reflect. The reflector tower utilized diode ambient light sensors to measure the amount of lumen. Lumen’s data is fed to the microcontroller and calculated by an algorithm to get the light’s direction vectors. A motor controls the whole tower from the vectors to get the maximum light for reflecting and charging the attached solar panel.

Various conditions cannot be tested due to environmental constraints such that the testing needs to be done in the earth’s surface environment rather than the moon. Certain environmental constraints, such as high temperature, must be adjusted when fabricated for the space environment. The material used can be less durable because of the earth’s atmosphere. Some parts used in the project must be considered in industrial form and alternative.

The moon has specific movement and hence has a different sun’s path. Such a constraint needed to be placed. The tower position needed to be strategically placed for the sun to have the highest reflection and reduce the amount of overhead pross path. On the earth's surface, the tower needed to be placed on the North-South axis and at an elevation higher than the target rovers and facilities. This facilitates the most amount of light, and there is no overhead path.

The mountains and craters on the moon are significantly higher than any elevation on the earth’s surface. Hence, the light path effectiveness must be scaled to appropriate intensity when fabricated for the space’s environment. An offset can be accounted for due to the minimal atmosphere interference on the moon. The project needed to consider lumen loss and changes in the light path in the earth's atmosphere. The battery needs to be able to last two weeks without sun. This needs to be the case for maximum sustainability for the mirror tower. This will allow for less reliance on the solar panels for charging by having a larger battery.

### 2.3.1.2 Wireless Charging/Docking Station – Stretch Goal:

For power, the main stretch goal for the communication tower would be a wireless charging component possibly with a docking station to allow for easier charging of the rover on the smaller tower that might have less capabilities for self-sustainability in terms of power. This would be a big boost for the accessibility of the rovers so that it could be operated remotely to be able to pick up the tower and bring it to a charging station. With this goal, it would disregard the need for cables to be plugged in or just relying on solar panels.

### 2.3.2 Software

### 2.3.2.1 Basic Goals

ASTROSCOPE must carry out multiple goals that comprise of electrical and computer science components. The main goal of the project is to be able to effectively reflect sunlight to a rover that might need sunlight or extra light to charge. To be able to do this, ASTROSCOPE must be able to communicate with these rovers using communication protocols to relay the message to the sensor and microcontroller to start this process. Our other main goal is to keep these two features, which are the mirror tower and the communication tower, separate from each other for functionality and mobility.

The main point of these two components being separate is so that the communication tower can be picked up and moved by a rover. This means that another one of our main goals is to have the communication tower be compact to the point that one of the rovers can theoretically pick it up and move it to a new location. Because of this, the communication tower must be able to relay the message to the mirror tower to using communication protocols to send the rover requests over. This can only be done by hosting a network, which is the primary goal of the communication tower.

In terms of light reflection, the first of the main goals for ASTROSCOPE are to identify the sun’s location by using algorithms with the light sensor and microcontroller to determine the optimal location for most light intensity. From here, ASTROSCOPE needs to calculate a vector for light trajectory to provide to the hardware’s movements with the motors. This movement of the motors will have to correspond with the specific coordinates of the rover in need of light.

For power, the main goals of ASTROSCOPE are to be sustainable and self-sufficient so that the towers can run on battery and solar power. From here, the towers will need to effectively deliver power to each component using a calculation software to determine which components are most important or in need of power on the towers. These power goals are critical for the functionality of ASTROSCOPE.

### 2.3.2.2 Peer to Peer Networking – Stretch Goal:

In the communication tower, there is a main stretch goal that is on the table if time permits. For the networking aspect, having a peer-to-peer network for each of the towers and to the rovers would be ideal to create a seamless communication system. The peer-to-peer networking system would allow for complete decentralization so there is no single point of failure between the rovers and communication tower. This would also allow for easy scalability for future additions to this project. Lastly, the peer-to-peer networking would add some extra security with no need for intermediary nodes.

## 2.4 Required Specifications

In consideration of objectives and constraints, specifications are required:

Table 0.1. Specification of Towers

Heliostat Tower
Minimum Temperature | -40°C
Reflector
Minimum size | 1ft diameter
Maximum size | 5ft diameter
Maximum Weight | 9kgs
Minimum Reflectivity | 98%
Response Time | 3 minutes
Tower Frame
Maximum total weight | 27kgs
Minimum Weight Capacity | 10kgs
Solar Panel
Minimum Power | 30W during sunlight hours
Maximum Voltage | 24V
Battery
Minimum Lifespan | 2 weeks without sun
Communication Tower
Minimum Enclosure Volume | 6.5"x6.5"x5"

Maximum Weight | 2kg
Minimum Network Range | 20m
Communication Rate | 2400MHz
Voltage input | 3.3V or 5V
Maximum Current Draw | 500mA
Minimum Temperature | -40°C
Latency | 1 second
Maximum Power | 5W


Figure 2.2. Hardware Diagram by Authors


Figure 2.2. Software Flowchart by Authors

## 2.5 House of Quality


Figure 2.4. House of Quality

## Chapter 10 - Administrative Content

## 10.1 Budget

The budget provided for this project is limited to $750. This limit is set by FSI and not by UCF or self-imposed. The goal of this project is to keep all costs within the $750 provided by FSI to minimize personal costs from group members.

Higher cost items, such as motors, microcontrollers, the frame, batteries, and solar panels, have been allocated a larger portion of the budget. Lower cost items such as regulators and sensors are allocated a smaller portion of the budget. Note the $750 budget includes multiple iterations, meaning the Bill of Materials must include room for spending on replacement or exchanged parts.

Table 10.1. The Budget allocation for the various parts of the project

Sub-System | Budget
PSU and Solar | $ 150.00
Frame/Reflector | $ 200.00
PCBs and Electrical | $ 100.00
Total | $ 450.00

Seen from the table above, this project is underbudget. This enables more margin for error, such as part replacement, and the iterative design process to take place without significant financial repercussions.

## 10.2 Bill of Materials

Table 10.2. An Itemized Bill of Materials

Component | Name | Price | Quantity
Mechanical
Mirror | 0.032" x 24" x 24", 3003-H14 Aluminum Sheet | $28.86 | 1
Mirror Coating | Mylar | $25.99 | 1
Frame | ADJ LTS-6 T-Bar Tripod Lightweight Lighting Stand | $54.99 | 1
Misc. | | ~$50
Electrical
Battery | Howell Energy hw-4f7 | 32.99 | 1
Motor w | Nema 23 | $30.73 | 1
Motor x-y-z | 9.5-11kg*cm Servo Motor | $0.00 | 0
Charge Controller/BMS | Smaraad SR11004 | $39.99 | 1
Mirror Coating | Mylar | $25.99 | 1
Solar Panel | RNG-50D-SS | $49.99 | 1
Microcontroller | ESP32-C6-DEVKITC-1-N8 | $9.00 | 1
External Antenna | PC140.07.0100A | $20.96 | 2
MicroSD card | 5251 | $4.50 | 2

MicroSD card breakout
board+
254 | $7.50 | 1

PCB
Microcontroller for PCB | ESP32-C6-WROOM-1U | $3.48 | 1
Stepper Motor Controller | DRV8833PW | $2.84 | 1
Servos Motor Controller | PCA9685PW,112 | $2.64 | 1
3.3V Regulator | TPS54JA20 | $1.50 | 1
5V Regulator | TPS54JA20 | $1.50 | 1
USB-A Connector | 2057-USB-AP-S-RA-SMT-ND | $0.55 | 3
Sensor-MUX | TCA9548APWR | $1.78 | 1
Sensor | VEML7700 | $1.88 | 5
USB-to-UART Bridge Controller | CP2102N-A02-GQFN28 | $4.07 | 1
MicroSD Socket | 1660 | $1.95 | 1
Misc. | | ~$20.00
Total | | $423.68

## 10.3 Distribution of Worktable

Below is the distribution of worktable detailing the assigned tasks to the group members. The responsibility of each system is distributed to specific members; however, each system relies on other member’s systems. Collaboration is present among the group members at every level of this project to ensure these systems are designed in a manner that they fit other system’s requirements. This ensures that all members are aware of and involved in the design and implementation of systems, regardless of if they are directly responsible for it or not.

Table 10.3. The distribution of worktable.

Electrical Engineering | Responsibilities
Alexandre Fiset | PSU Design and Implementation
PCB Design
MPPT Tracking Implementation Administrative Documentation
Computer Engineering | Responsibilities
Binh Pham | Reflector Technology and Design
Motor and Motor Controls
Vectoring Technology
Project Lead
Positioning and Vectoring Algorithm
Computer Engineering | Responsibilities
Pedro Kasprzykowski | MCU Selection and Implementation
Software Design and Implementation

Antenna and Communications Website Design and Management

Computer Engineering | Responsibilities
Stephen Martin | Sensor Selection and Implementation
MCU Selection and Implementation Positioning and Vectoring Algorithm Software Design and Implementation

## 10.4 Milestones

Multiple events and meeting are required to create a good dynamic between members and a successful project. First, new members are recruited, and project’s topics discussion held in the first week of senior design I to kick start the project with sufficient information:

Table 10.4. Project Initialization Milestone

Project Initialization
Start Date | Planed Date | Required End Date | Task | Description
08/21/2023 | 08/21/2023 | 08/21/2023 | Recruiting | Members recruited: Alexandre Fiset (EE), Pedro Kasprzykowski (CpE), Stephen Martin (CpE), Binh Pham (CPE)
08/22/2023 | 08/29/2023 | 08/29/2023 | Brainstorming | Meeting in person to go over various ideas and pick one for the project.
08/30/2023 | 08/30/2023 | 08/30/2023 | Sponsor Meeting | Discuss idea with sponsor.
08/28/2023 | 09/04/2023 | 09/15/2023 | Initial Document | First 10 pages of Divide and Conquer
08/28/2023 | 10/28/2023 | 11/03/2023 | 60-Page Milestone | First have of the Document
08/28/2023 | 12/01/2023 | 12/05/2023 | Final Document | Final Document of SD I

Table 10.5. Project Fabrication Milestone

Project Fabrication
Start Date | Planed Date | Required End Date | Task | Description
08/28/2023 | 09/28/2023 | 09/28/2023 | Components Selection | Making a tentative BOM with core component
09/13/2023 | 10/29/2023 | 12/05/2023 | System Design | Making overall schematic for the project

10/29/2023 | 12/01/2023 | 12/05/2023 | System Testing | Testing individual component and compatibility
10/29/2023 | 11/15/2023 | TBD-SDII | PCB Design | Discuss idea with sponsor.
TBD-SDII | TBD-SDII | TBD-SDII | PCB Testing | First have of the Document
TBD-SDII | TBD-SDII | TBD-SDII | Prototype Completion | Final Document of SD I

Various tasks are overlap as expecting due to the nature of the project and some tasks are TBD. This milestone is a guideline for reference as a successful project.

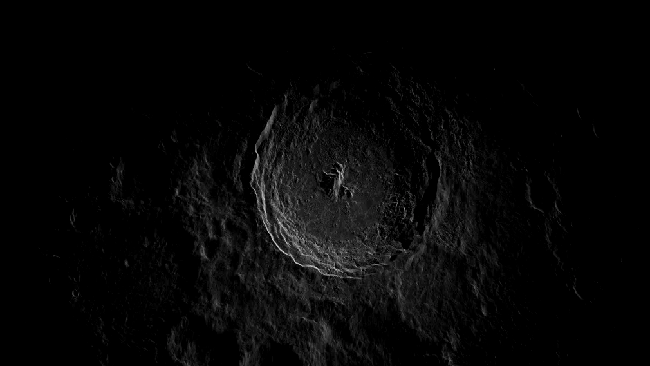
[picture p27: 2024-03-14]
software/website/img/moon.png

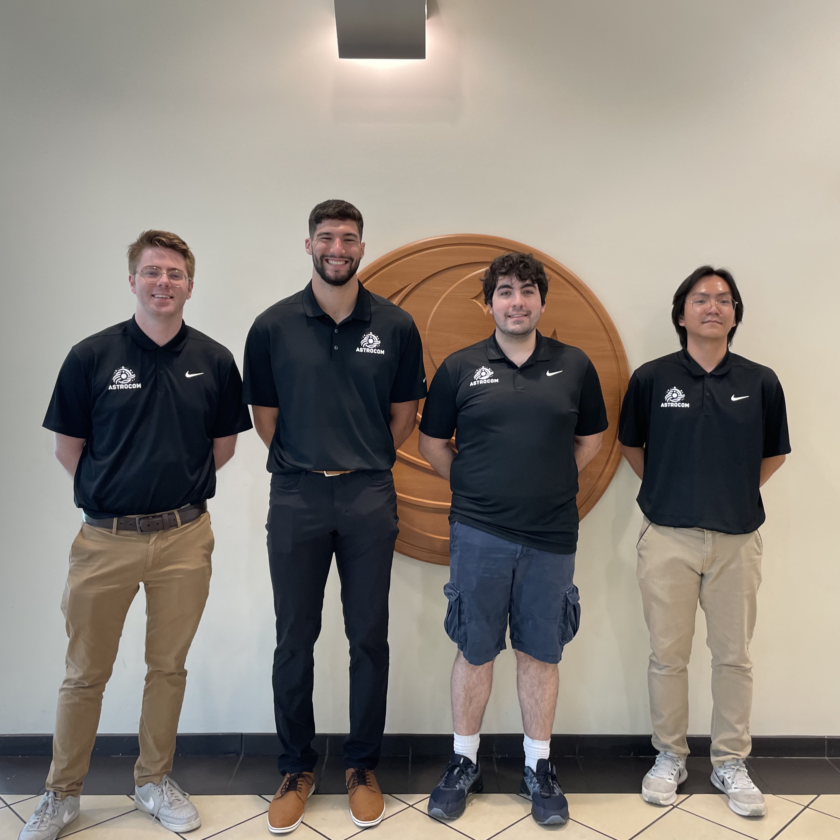
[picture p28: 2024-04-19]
software/website/img/seal_pic.jpg

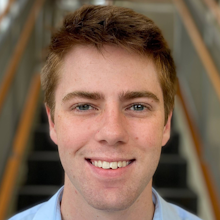
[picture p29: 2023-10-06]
software/website/img/alex.png

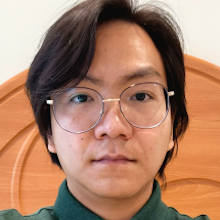
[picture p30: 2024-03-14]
software/website/img/binh.png

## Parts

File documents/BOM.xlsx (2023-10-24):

Description | Manufacturer | Value | Availability | Price (from) | Quantity | Total Price | Order code | Manuf. Code | Order Request date | Links
0.032" x 24" x 24", 3003-H14 Aluminum Sheet | Online Metal Supply | 2ftx2ftx0.032" | 12 | $28.86 | 1 | $28.86 | - | - | 2023-10-24 | https://www.amazon.com/ (https://www.amazon.com/0-032-3003-H14-Aluminum-Sheet-Mill/dp/B0BGLBD2Q7/)
VIVOSUN Highly Reflective Mylar Film Roll 4FT x 25FT | VIVOSUN | 4FT x 25FT | 11 | $25.99 | 1 | $25.99 | - | - | 2023-10-24 | https://www.amazon.com/ (https://www.amazon.com/VIVOSUN-Horticulture-Highly-Reflective-Mylar/dp/B018VI75CS?hvadid=409979484237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)
ADJ Products LTS-6, Par Can Tripod(9 FT) | ADJ | 6-9ft | In Stock | $54.99 | 1 | $54.99 | - | - | 2023-10-24 | https://www.amazon.com/ (https://www.amazon.com/ADJ-Products-LTS-6-METAL-CROSSBAR/dp/B00KFZAPBE)
Smaraad 10 Amp Solar Charge Controller MPPT | Smaraad renewable | 10A-2V/24V | In Stock | $35.99 | 1 | $35.99 | - | - | 2023-10-24 | https://www.amazon.com/ (https://www.amazon.com/Smaraad-Controller-Detection-Adjustable-Display/dp/B0BZD3HKMH)
HWE 12V 7Ah Battery, 12V Lithium Battery | HWE | 12V 7Ah | In Stock | $32.99 | 1 | $32.99 | - | - | 2023-10-24 | https://www.amazon.com/ (https://www.amazon.com/Battery-HWE-Lithium-LiFePO4-Outdoor/dp/B095K38M6C)
Nema 23 CNC Stepper Motor 2.8A 178.4oz.in/1.26Nm | STEPPERONLINE | 2.8A 178.4oz.in/1.26Nm | In Stock | $30.73 | 1 | $30.73 | - | - | 2023-10-24 | https://www.amazon.com/ (https://www.amazon.com/STEPPERONLINE-Stepper-178-5oz-1-26Nm-Stepping/dp/B00PNEPF5I)
Renogy 50 Watt 12 Volt Monocrystalline Solar Panel | Regnogy | 50 Watt 12 Volt | In Stock | $39.99 | 1 | $39.99 | - | - | 2023-10-24 | https://www.amazon.com/ (https://www.amazon.com/Renogy-Monocrystalline-Efficiency-Charging-Applications/dp/B07GTH79JP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)
Rear Wheel Hub and Bearing Assembly | Bodeman | 7.7 Pounds | 4 | $44.90 | 1 | $44.90 | - | - | 2023-10-24 | https://www.amazon.com/ (https://www.amazon.com/Bodeman-Bearing-Assembly-2009-2015-Highlander/dp/B07VHKV6BV)
Junction Box ABS Plastic Dustproof Waterproof IP65 | Zulkit | 8.7 x 6.7 x 4.3 inch | In Stock | $26.89 | 1 | 26.89 | - | - | 2023-10-24 | https://www.amazon.com/ (https://www.amazon.com/Zulkit-Waterproof-Electrical-Transparent-220x170x110/dp/B07RVN91WB)
ESP32-C ESP32-C6-WROOM-1 Transceiver; 802.15.4 | Espressif Systems | Board(s) | 778 | $9.00 | 1 | $9.00 | 1965-ESP32-C6-DEVKITC-1-N8-ND | ESP32-C6-DEVKITC-1-N8 | 2023-10-24 | https://www.digikey.com/ (https://www.digikey.com/en/products/detail/espressif-systems/ESP32-C6-DEVKITC-1-N8/17728861)
Memory Card microSD™ 256MB Class 4 | Adafruit Industries LLC | 256MB | 37 | $4.50 | 2 | $9.00 | 1528-5251-ND | 5251 | 2023-10-24 | https://www.digikey.com/ (https://www.digikey.com/en/products/detail/adafruit-industries-llc/5251/15841479)
MICROSD CARD BREAKOUT 5V OR 3V | Adafruit Industries LLC | 1.254" L x 1.000" W | 288 | $7.50 | 1 | $7.50 | 1528-1462-ND | 254 | 2023-10-24 | https://www.digikey.com/ (https://www.digikey.com/en/products/detail/adafruit-industries-llc/254/5761230)
2.45GHz Bluetooth, ISM, Wi-Fi PCB Trace RF Antenna | Taoglas Limited | 2.4GHz ~2.5GHz | 56 | $21.81 | 2 | $43.62 | 931-1552-ND | PC140.07.0100A | 2023-10-24 | https://www.digikey.com/ (https://www.digikey.com/en/products/detail/taoglas-limited/PC140-07-0100A/9972815)
3/8-in x 4-ft x 8-ft Pine Plywood Sheathing | - | 3/8"x4'x8' | In Stock | $25.60 | 2 | $51.20 | - | - | 2023-10-24 | https://www.lowes.com/ (https://www.lowes.com/pd/Plytanium-3-8-CAT-PS1-09-Square-Structural-Plywood-Pine-Application-as-4-x-8/1000068943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)
PCB Budget | - | - | - | $150 | 1 | $150.00 | - | - | TBA
Extended Budget | - | - | - | $150 | 1 | $150.00 | - | - | TBA
 |  |  |  |  |  | $741.65

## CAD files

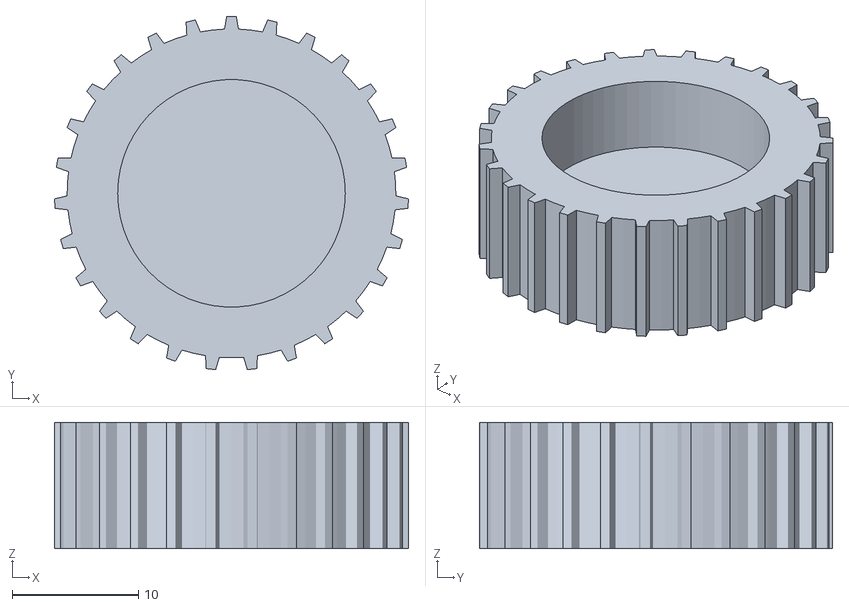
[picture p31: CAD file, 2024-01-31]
hardware/cad/dxf/CV_Axle_V1.stl.dxf
28.0 x 27.9 x 10.0

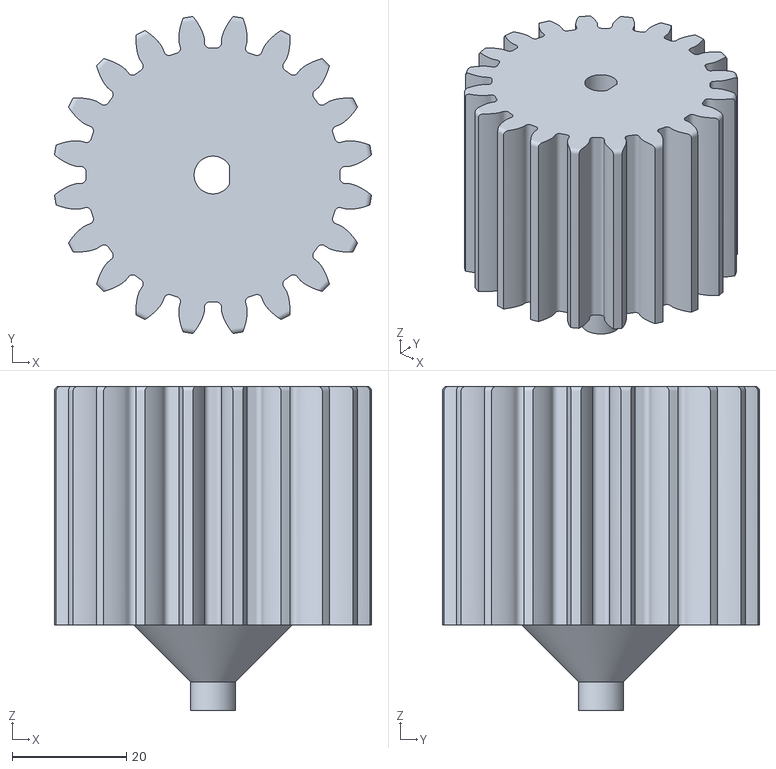
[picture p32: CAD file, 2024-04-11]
hardware/cad/STL/Gear_Stepper_V4.stl
55.4 x 55.4 x 56.8

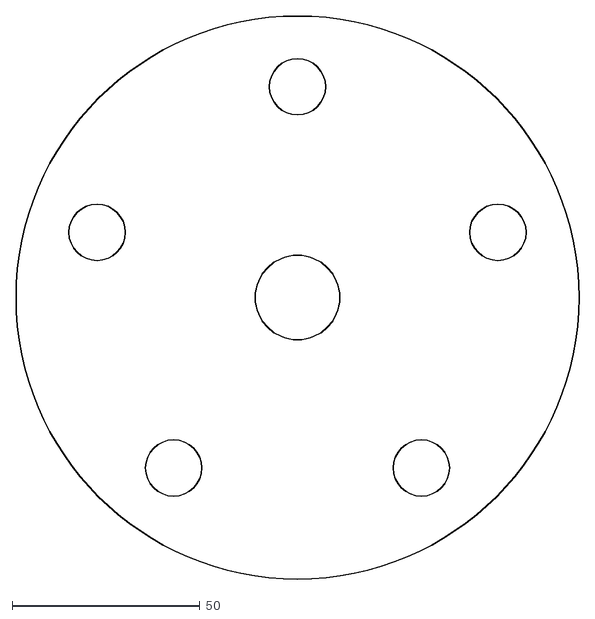
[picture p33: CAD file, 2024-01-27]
hardware/cad/dxf/Spring_holder.dxf
150.0 x 150.0

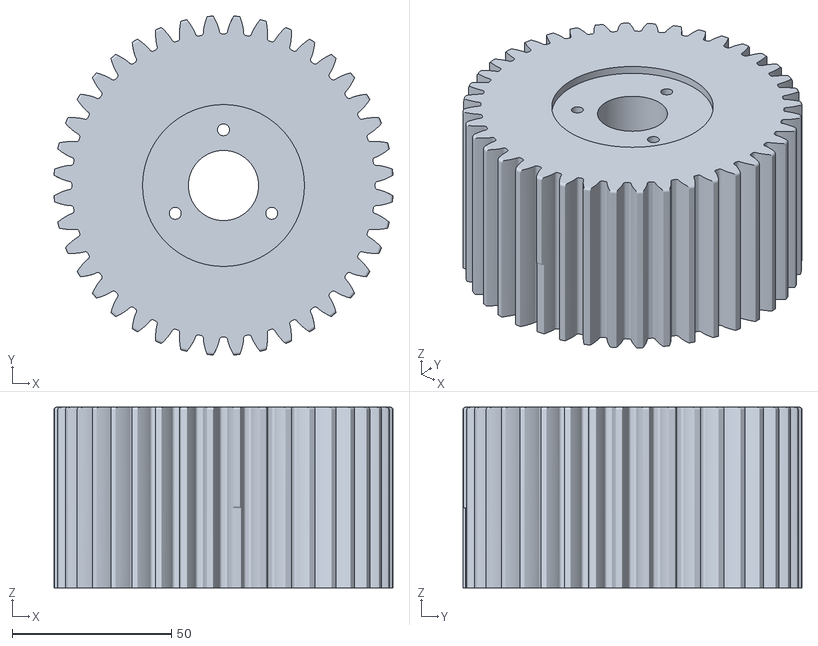
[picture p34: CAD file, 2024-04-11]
hardware/cad/STL/Gear_Base_V4.stl
106.5 x 106.5 x 56.7

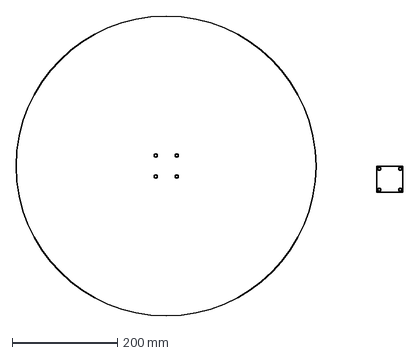
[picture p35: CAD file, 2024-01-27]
hardware/cad/dxf/Mirror_Cutting.dxf
735.0 x 570.0 mm

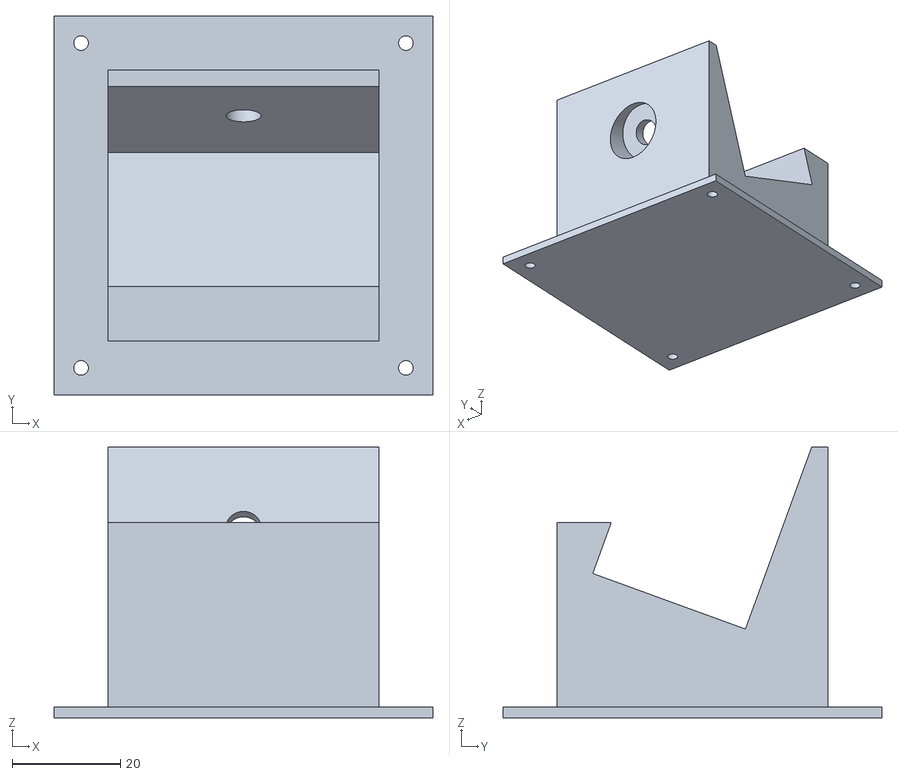
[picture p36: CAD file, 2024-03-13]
hardware/cad/STL/Solar_Panel_Stand.stl
70.0 x 70.0 x 50.0

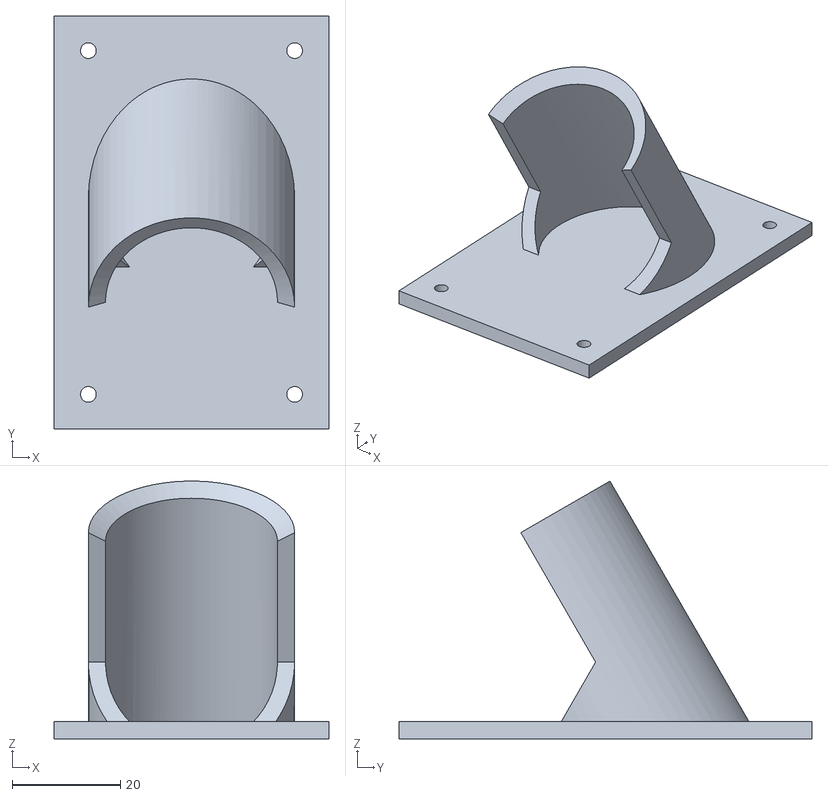
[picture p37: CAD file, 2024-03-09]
hardware/cad/STL/Leg_Holder.stl
50.8 x 76.2 x 47.6

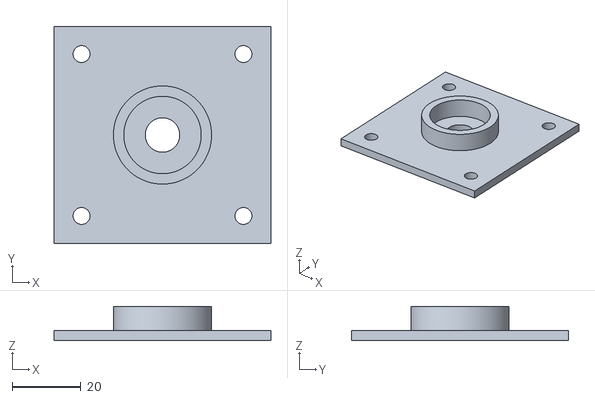
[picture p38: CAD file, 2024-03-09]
hardware/cad/STL/Stepper_Housing_Lid.stl
63.0 x 63.0 x 10.0

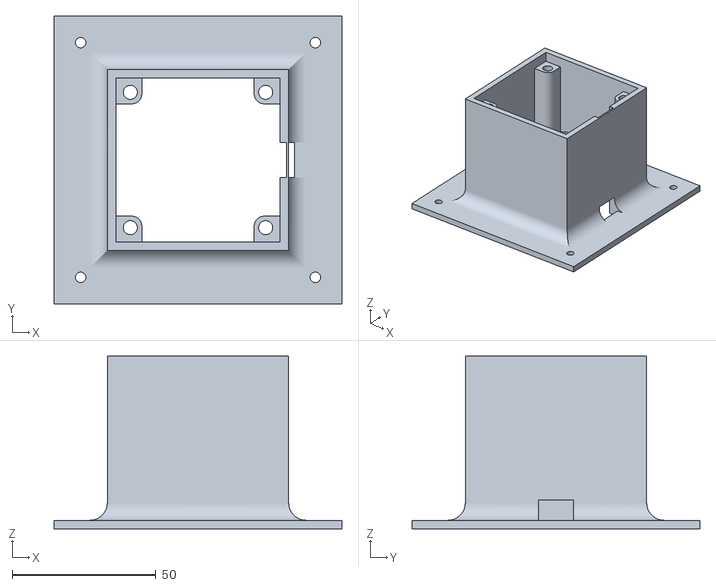
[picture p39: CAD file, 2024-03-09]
hardware/cad/STL/Stepper_Housing_Base.stl
100.0 x 100.0 x 60.0

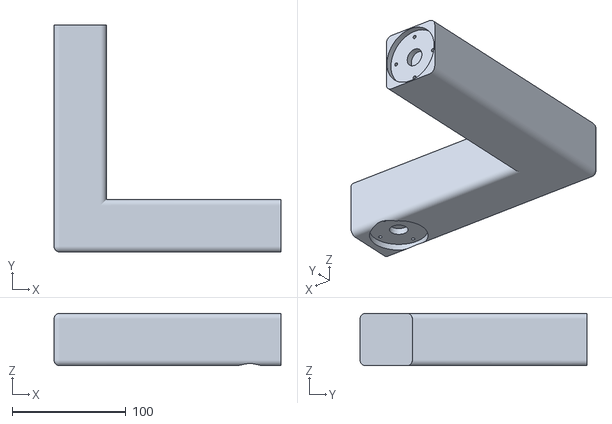
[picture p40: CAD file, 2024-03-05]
hardware/cad/STL/Reflector_L_Piece.stl
200.0 x 200.0 x 46.2

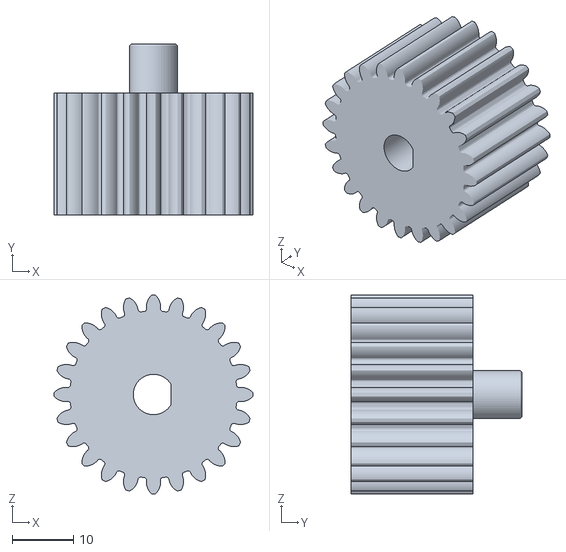
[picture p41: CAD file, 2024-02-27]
hardware/cad/STL/Stepper_Gear.stl
32.5 x 28.0 x 32.5

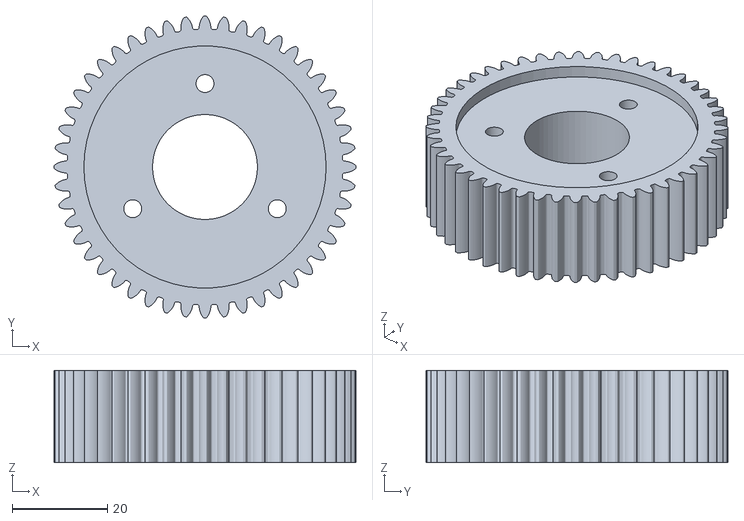
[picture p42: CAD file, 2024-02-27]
hardware/cad/STL/Gear_for_Axle.stl
63.3 x 63.3 x 19.3

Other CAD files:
hardware/cad/dwg/Sensor_Housing.dwg
hardware/cad/Step/Axel.step
hardware/cad/dwg/CommTower.dwg
hardware/cad/dwg/BottomHousing_NEW.dwg
hardware/cad/dwg/Servo_Board_Housing.dwg
hardware/cad/dwg/Reflector.dwg
hardware/cad/STL/Archived/CV_Axle.stl
hardware/cad/STL/Archived/DS3225_Servo_Bearing_1.stl
hardware/cad/STL/Archived/DS3225_Servo_Bearing_2.stl
hardware/cad/STL/Archived/Gear_Base_V2.stl
hardware/cad/STL/Archived/Gear_Base_V3.stl
hardware/cad/STL/Archived/Gear_for_Stepper.stl
hardware/cad/STL/Archived/STAND2.stl
hardware/cad/STL/Archived/Servo_Board_Housing_1.stl
hardware/cad/STL/Archived/Stand1(1).stl
hardware/cad/STL/Archived/stand1.stl
hardware/cad/STL/Axle.stl
hardware/cad/STL/CV_Axle.stl
hardware/cad/STL/DS3225_Servo_Bearing_1.stl
hardware/cad/STL/DS3225_Servo_Bearing_2.stl
hardware/cad/STL/Gear_Base_V2.stl
hardware/cad/STL/Gear_Base_V3.stl
hardware/cad/STL/Gear_for_Stepper.stl
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

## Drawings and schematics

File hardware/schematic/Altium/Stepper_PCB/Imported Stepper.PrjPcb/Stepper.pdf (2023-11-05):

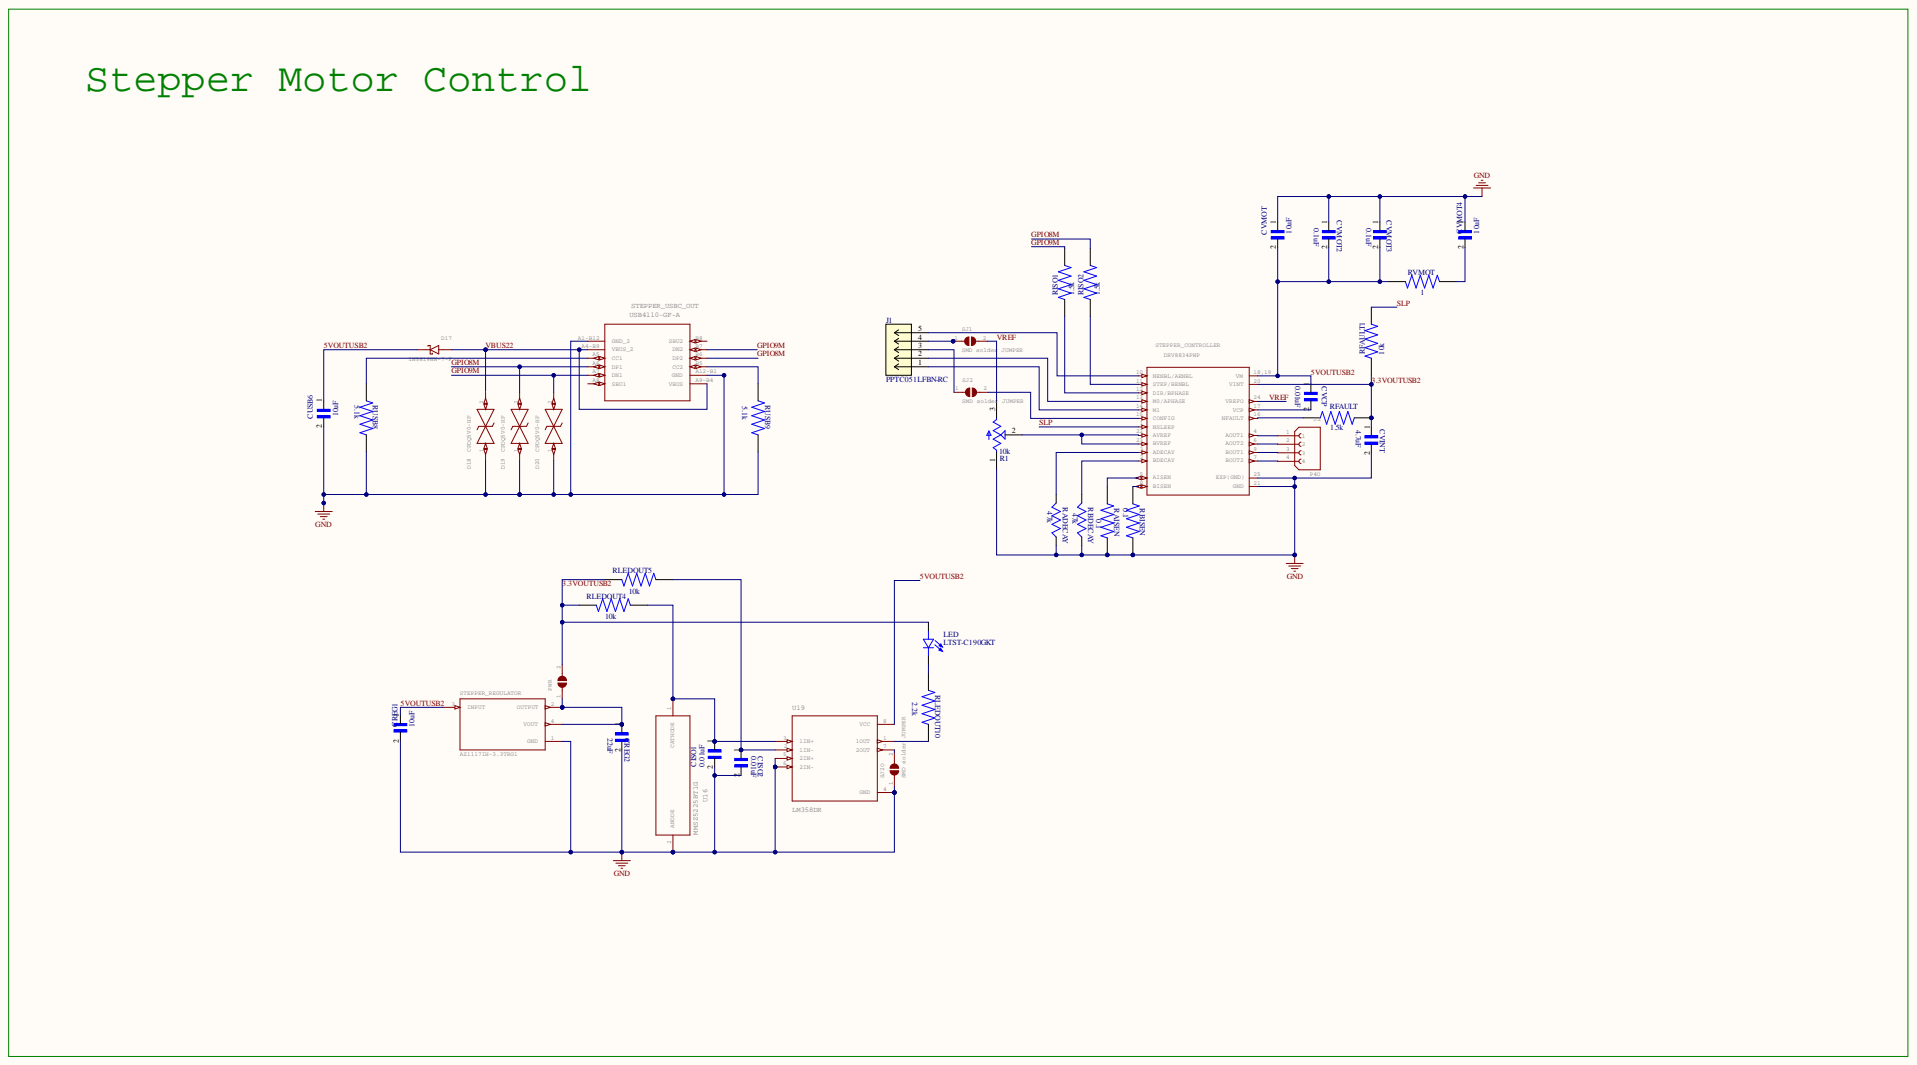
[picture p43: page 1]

4 | 1 2 VREF

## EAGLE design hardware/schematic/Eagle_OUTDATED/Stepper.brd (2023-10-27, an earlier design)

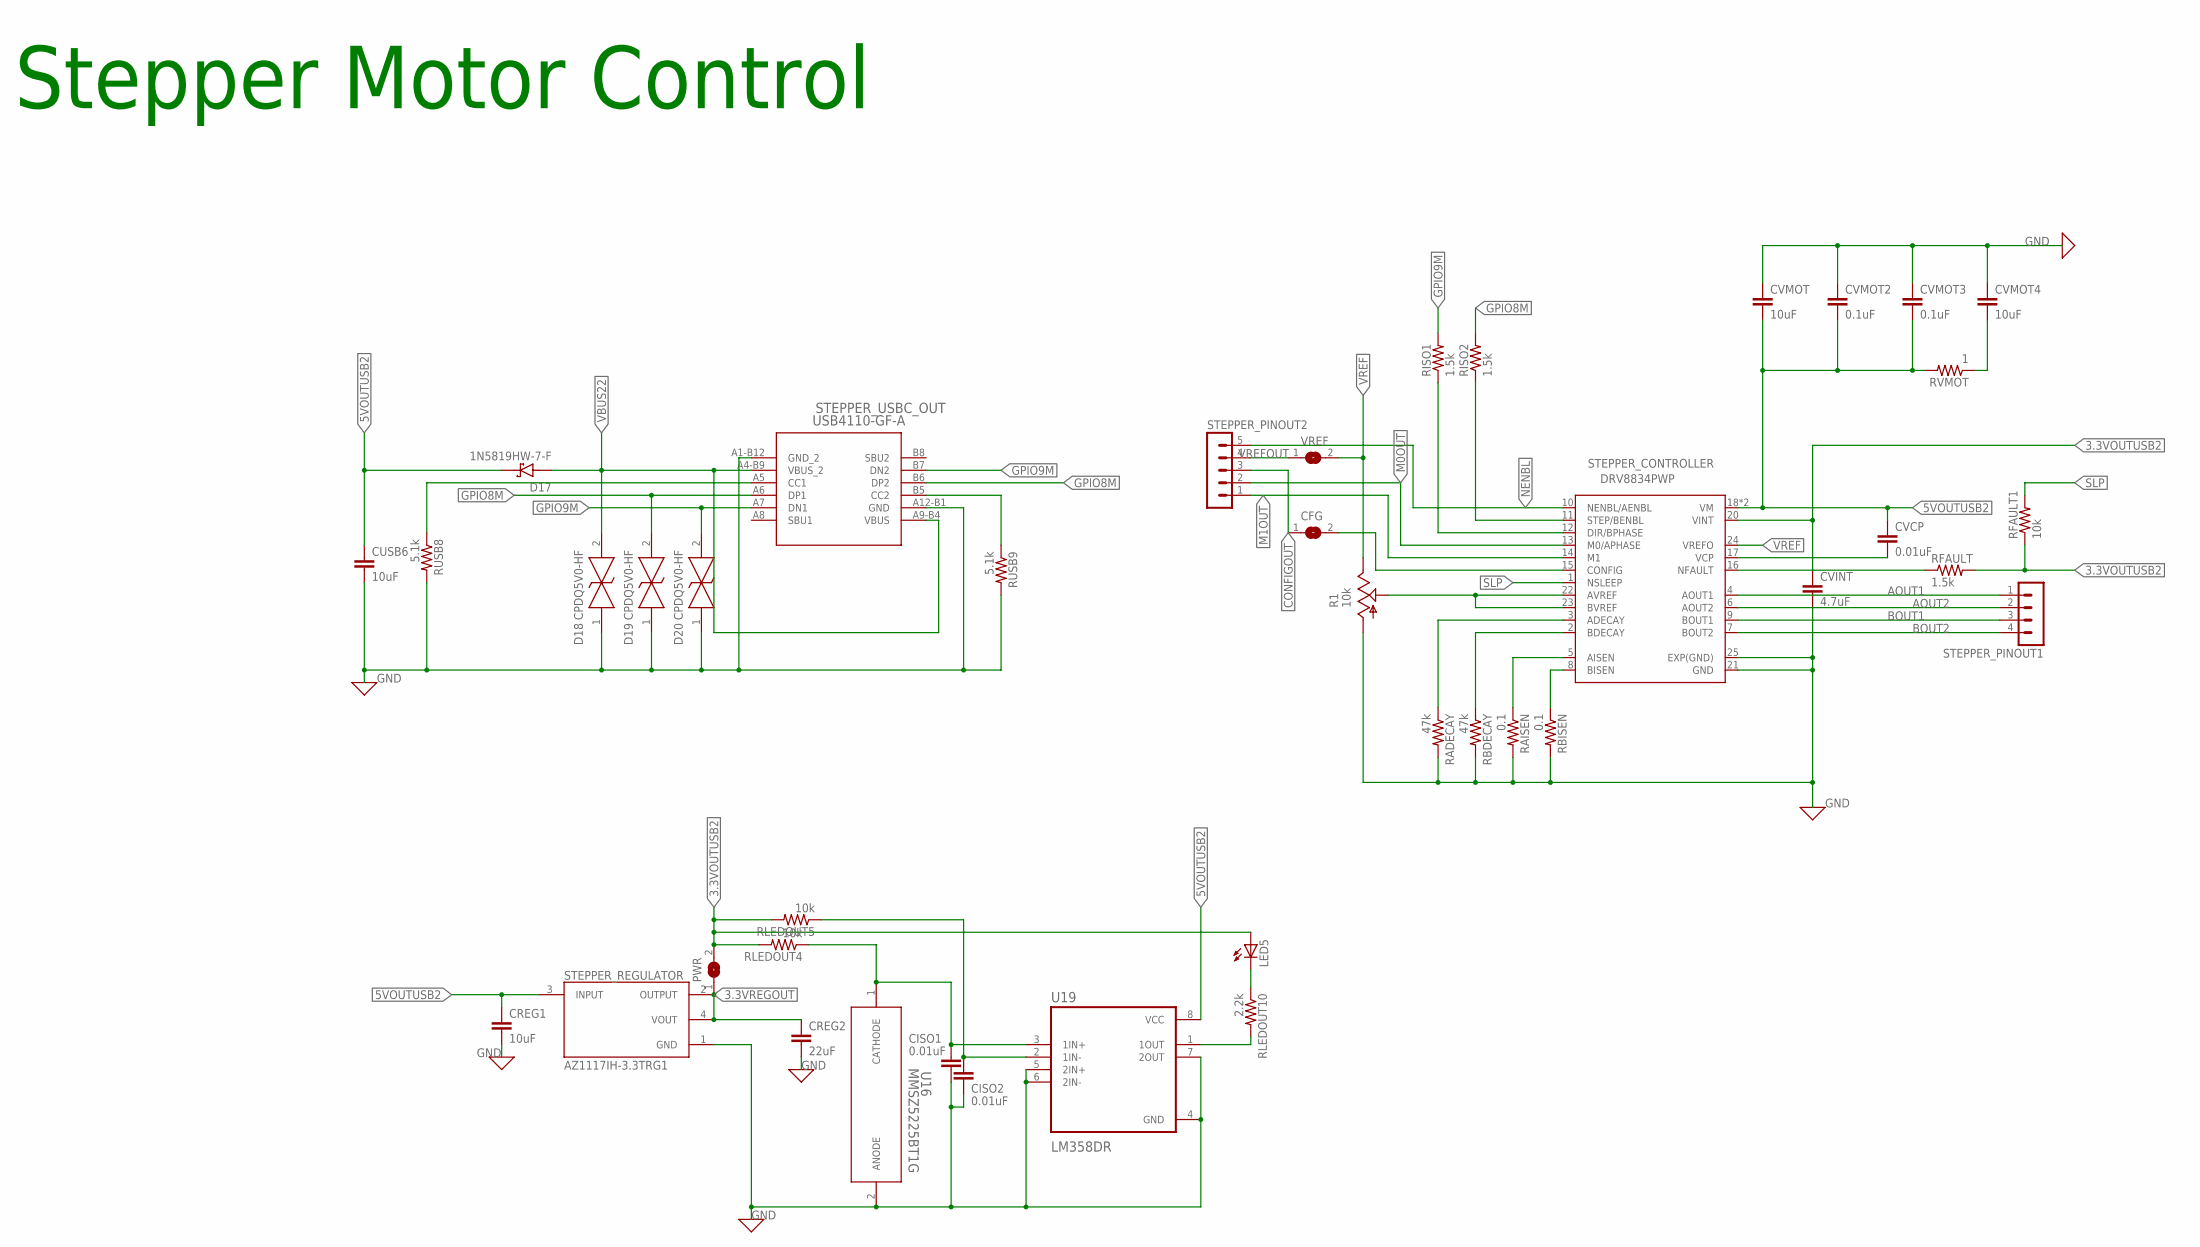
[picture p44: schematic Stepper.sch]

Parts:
CFG: SJ
CISO1, CISO2: 0.01uF; C0805
CREG1: 10uF; C0805
CREG2: 22uF; C0805
CUSB6: 10uF; C0805
CVCP: 0.01uF; C0805
CVINT: 4.7uF; C0805
CVMOT, CVMOT4: 10uF; C0805
CVMOT2, CVMOT3: 0.1uF; C0805
D17: 1N5819HW-7-F; SOD3715X145N
D18, D19, D20: CPDQ5V0-HF; MBTB-D-SOD-923F-IMP-0402
LED5: LED; SMARTLED-TTW
PWR: SJ
R1: 10k; 3223G
RADECAY: 47k; M0805
RAISEN: 0.1; M0805
RBDECAY: 47k; M0805
RBISEN: 0.1; M0805
RFAULT: 1.5k; M0805
RFAULT1: 10k; M0805
RISO1, RISO2: 1.5k; M0805
RLEDOUT4, RLEDOUT5: 10k; M0805
RLEDOUT10: 2.2k; M0805
RUSB8, RUSB9: 5.1k; M0805
RVMOT: 1; M0805
STEPPER_CONTROLLER: DRV8834PWP; SOP65P640X120-25N
STEPPER_PINOUT1: MA04-1
STEPPER_PINOUT2: MA05-1
STEPPER_REGULATOR: AZ1117IH-3.3TRG1; SOT230P700X185-4N
STEPPER_USBC_OUT: USB4110-GF-A; USB4110-GF-A_GCT
U16: MMSZ5225BT1G; SOD-123_ONS
U19: LM358DR; SOIC127P599X175-8N
VREF: SJ

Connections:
3.3VOUTUSB2: CVINT.1, LED5.A@1 (A), PWR.2, RFAULT.2, RFAULT1.1, RLEDOUT4.2, RLEDOUT5.2, STEPPER_CONTROLLER.20 (VINT)
3.3VREGOUT: CREG2.1, PWR.1, STEPPER_REGULATOR.2 (OUTPUT), STEPPER_REGULATOR.4 (VOUT)
5VOUTUSB2: CREG1.1, CUSB6.1, CVCP.1, CVMOT.2, CVMOT2.2, CVMOT3.2, D17.C (K), RVMOT.2, STEPPER_CONTROLLER.18 (VM), STEPPER_CONTROLLER.19 (VM), STEPPER_REGULATOR.3 (INPUT), U19.8 (VCC)
AOUT1: STEPPER_CONTROLLER.4 (AOUT1), STEPPER_PINOUT1.1
AOUT2: STEPPER_CONTROLLER.6 (AOUT2), STEPPER_PINOUT1.2
BOUT1: STEPPER_CONTROLLER.9 (BOUT1), STEPPER_PINOUT1.3
BOUT2: STEPPER_CONTROLLER.7 (BOUT2), STEPPER_PINOUT1.4
CONFIGOUT: CFG.1, STEPPER_PINOUT2.3
GND: CISO1.2, CISO2.2, CREG1.2, CREG2.2, CUSB6.2, CVINT.2, CVMOT.1, CVMOT2.1, CVMOT3.1, CVMOT4.1, D18.1 (K), D19.1 (K), D20.1 (K), R1.1 (A), RADECAY.2, RAISEN.2, RBDECAY.2, RBISEN.2, RUSB8.2, RUSB9.2, STEPPER_CONTROLLER.21 (GND), STEPPER_CONTROLLER.25 (EXP(GND)), STEPPER_REGULATOR.1 (GND), STEPPER_USBC_OUT.A1-B12 (GND_2), STEPPER_USBC_OUT.A12-B1 (GND), U16.2 (ANODE), U19.4 (GND), U19.5 (2IN+), U19.6 (2IN-), U19.7 (2OUT)
GPIO8M: D19.2 (A), RISO2.2, STEPPER_USBC_OUT.A6 (DP1), STEPPER_USBC_OUT.B6 (DP2)
GPIO9M: D20.2 (A), RISO1.2, STEPPER_USBC_OUT.A7 (DN1), STEPPER_USBC_OUT.B7 (DN2)
M0OUT: STEPPER_CONTROLLER.13 (M0/APHASE), STEPPER_PINOUT2.2
M1OUT: STEPPER_CONTROLLER.14 (M1), STEPPER_PINOUT2.1
unnamed: RISO1.1, STEPPER_CONTROLLER.12 (DIR/BPHASE)
unnamed: RISO2.1, STEPPER_CONTROLLER.11 (STEP/BENBL)
unnamed: CVMOT4.2, RVMOT.1
unnamed: RBISEN.1, STEPPER_CONTROLLER.8 (BISEN)
unnamed: RAISEN.1, STEPPER_CONTROLLER.5 (AISEN)
unnamed: RBDECAY.1, STEPPER_CONTROLLER.2 (BDECAY)
unnamed: RADECAY.1, STEPPER_CONTROLLER.3 (ADECAY)
unnamed: RFAULT.1, STEPPER_CONTROLLER.16 (NFAULT)
unnamed: CVCP.2, STEPPER_CONTROLLER.17 (VCP)
unnamed: R1.2 (S), STEPPER_CONTROLLER.22 (AVREF), STEPPER_CONTROLLER.23 (BVREF)
unnamed: CFG.2, STEPPER_CONTROLLER.15 (CONFIG)
unnamed: RUSB8.1, STEPPER_USBC_OUT.A5 (CC1)
unnamed: RUSB9.1, STEPPER_USBC_OUT.B5 (CC2)
unnamed: CISO1.1, RLEDOUT4.1, U16.1 (CATHODE), U19.3 (1IN+)
unnamed: CISO2.1, RLEDOUT5.1, U19.2 (1IN-)
unnamed: RLEDOUT10.2, U19.1 (1OUT)
unnamed: LED5.C@1 (C), RLEDOUT10.1
NENBL: STEPPER_CONTROLLER.10 (NENBL/AENBL), STEPPER_PINOUT2.5
SLP: RFAULT1.2, STEPPER_CONTROLLER.1 (NSLEEP)
VBUS22: D17.A, D18.2 (A), STEPPER_USBC_OUT.A4-B9 (VBUS_2), STEPPER_USBC_OUT.A9-B4 (VBUS)
VREF: R1.3 (E), STEPPER_CONTROLLER.24 (VREFO), VREF.2
VREFOUT: STEPPER_PINOUT2.4, VREF.1

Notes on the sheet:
Stepper Motor Control

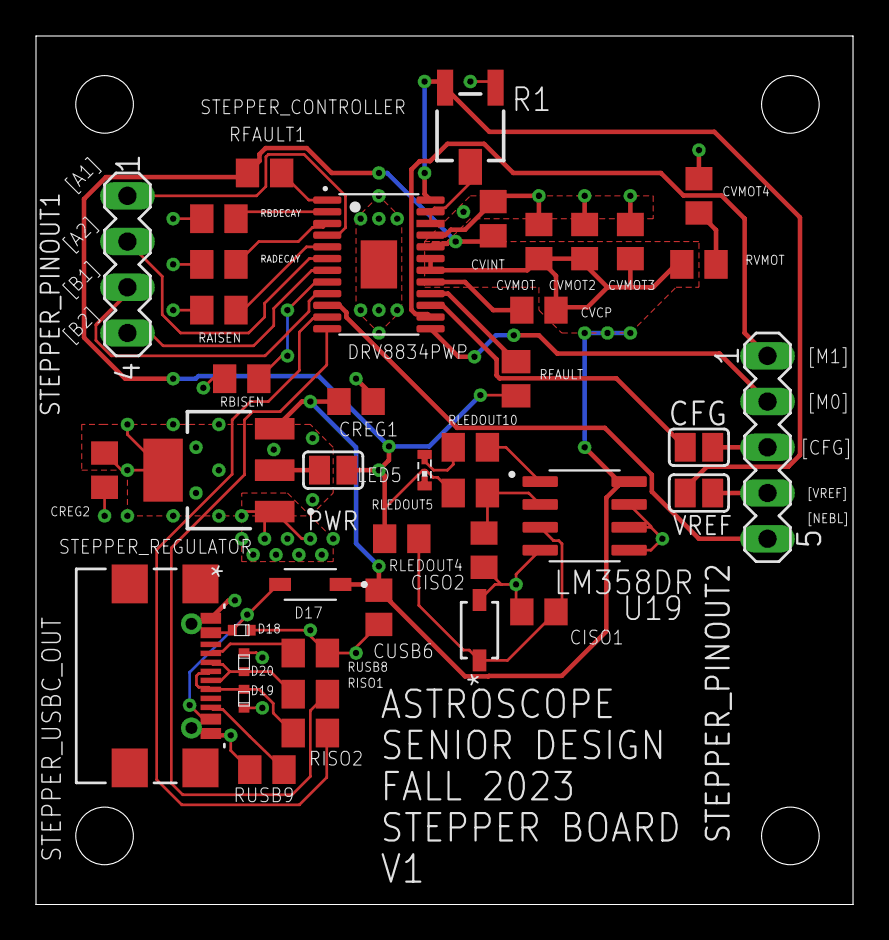
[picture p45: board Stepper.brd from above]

Board: 2 copper layers, 45.4 x 48.2 mm, 41 parts (0 on the bottom side), 35 nets.

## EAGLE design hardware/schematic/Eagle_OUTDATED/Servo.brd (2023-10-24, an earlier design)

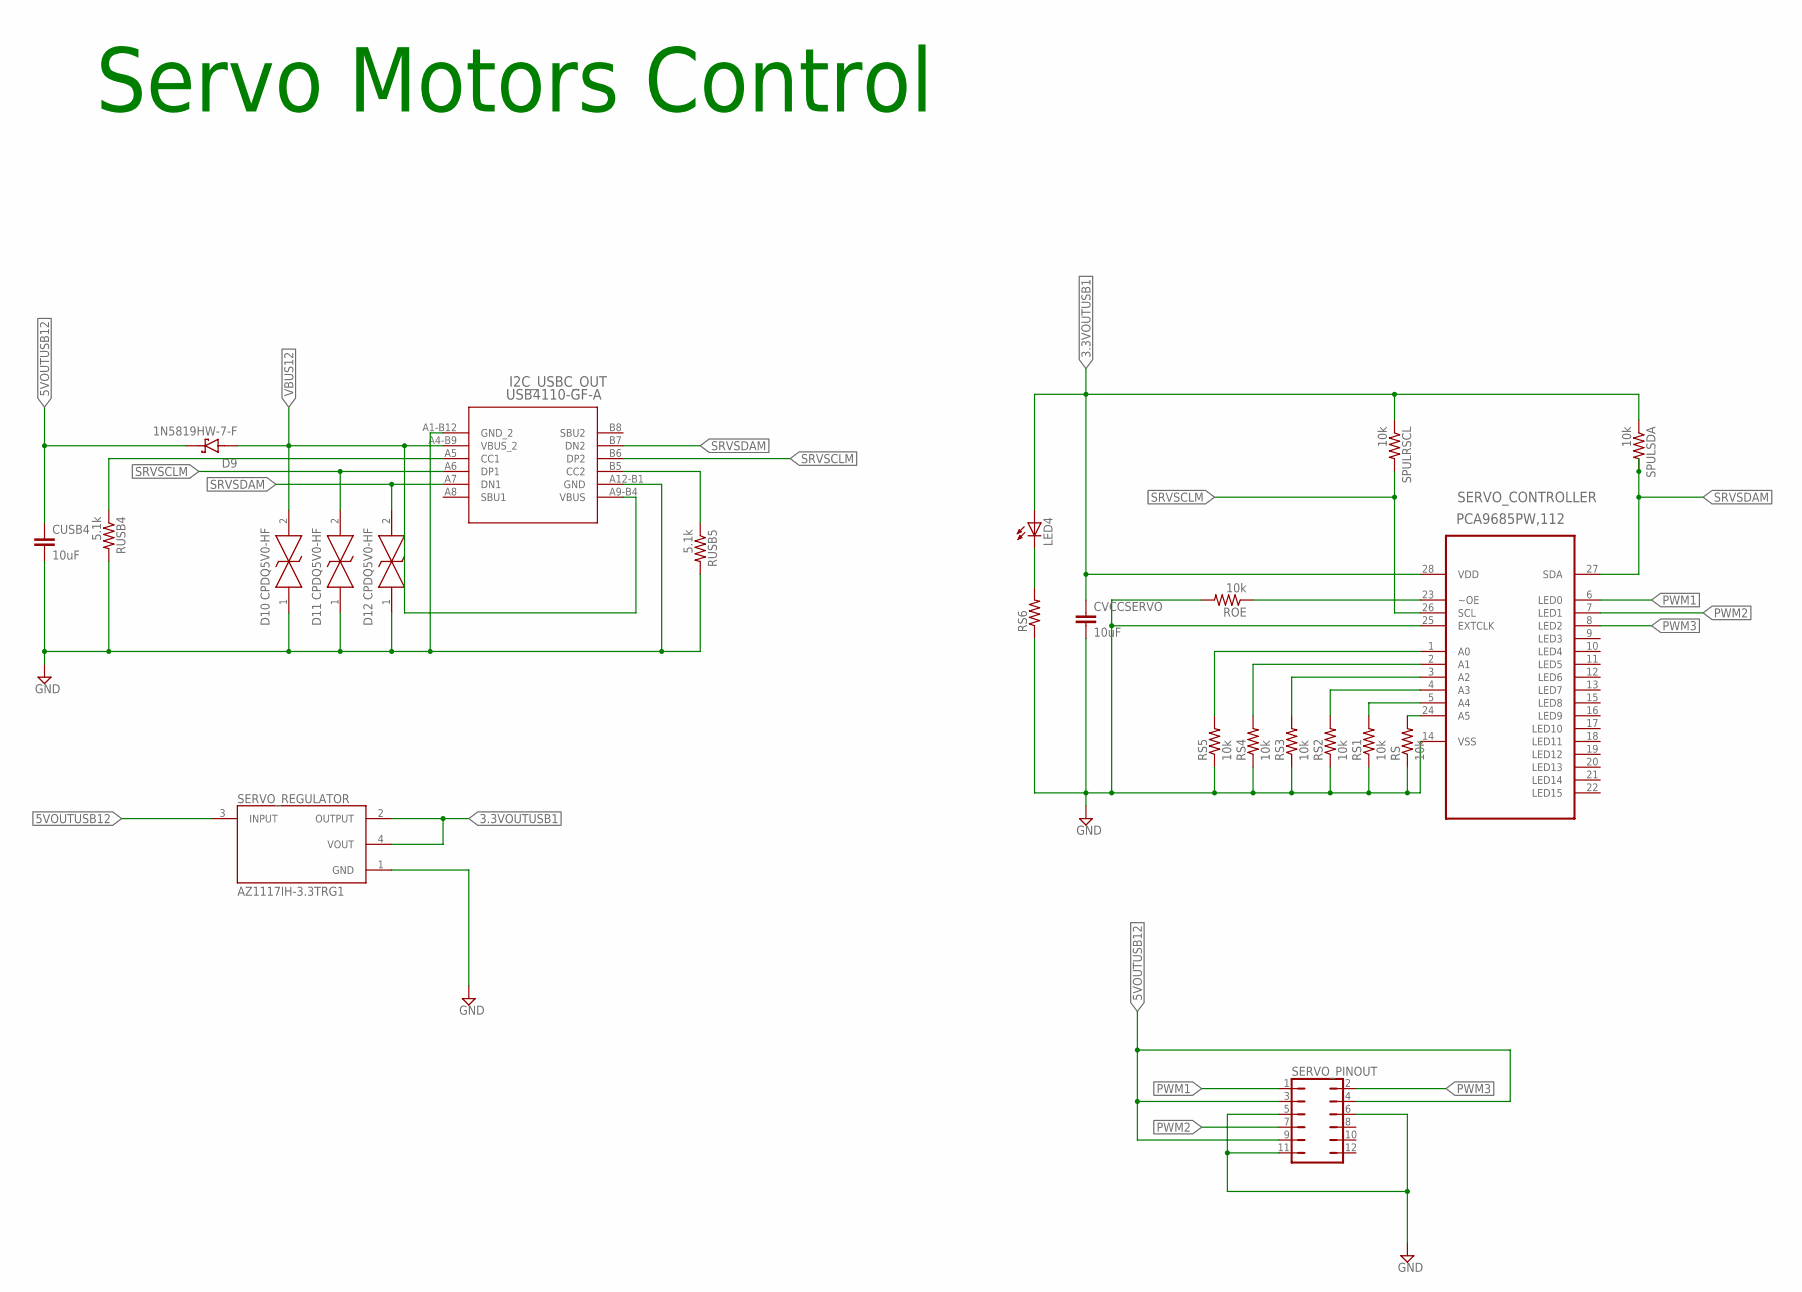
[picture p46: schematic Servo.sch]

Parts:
CUSB4: 10uF; C0805
CVCCSERVO: 10uF; C0805
D9: 1N5819HW-7-F; SOD3715X145N
D10, D11, D12: CPDQ5V0-HF; MBTB-D-SOD-923F-IMP-0402
I2C_USBC_OUT: USB4110-GF-A; USB4110-GF-A_GCT
LED4: LED; SMARTLED-TTW
ROE: 10k; M0805
RS, RS1, RS2, RS3, RS4, RS5: 10k; R0805
RS6: 2.2k; R0805
RUSB4, RUSB5: 5.1k; M0805
SERVO_CONTROLLER: PCA9685PW,112; SOP65P640X110-28N
SERVO_PINOUT: JP6Q
SERVO_REGULATOR: AZ1117IH-3.3TRG1; SOT230P700X185-4N
SPULRSCL: 10k; M0805
SPULSDA: 10k; M0805

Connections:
3.3VOUTUSB1: CVCCSERVO.1, LED4.A@1 (A), SERVO_CONTROLLER.28 (VDD), SERVO_REGULATOR.2 (OUTPUT), SERVO_REGULATOR.4 (VOUT), SPULRSCL.1, SPULSDA.1
5VOUTUSB12: CUSB4.1, D9.C (K), SERVO_PINOUT.3, SERVO_PINOUT.4, SERVO_PINOUT.9, SERVO_REGULATOR.3 (INPUT)
A0: RS5.2, SERVO_CONTROLLER.1 (A0)
A1: RS4.2, SERVO_CONTROLLER.2 (A1)
A2: RS3.2, SERVO_CONTROLLER.3 (A2)
A3: RS2.2, SERVO_CONTROLLER.4 (A3)
A4: RS1.2, SERVO_CONTROLLER.5 (A4)
A5: RS.2, SERVO_CONTROLLER.24 (A5)
CC1_RUSB4: I2C_USBC_OUT.A5 (CC1), RUSB4.1
CC2: I2C_USBC_OUT.B5 (CC2), RUSB5.1
GND: CUSB4.2, CVCCSERVO.2, D10.1 (K), D11.1 (K), D12.1 (K), I2C_USBC_OUT.A1-B12 (GND_2), I2C_USBC_OUT.A12-B1 (GND), ROE.2, RS.1, RS1.1, RS2.1, RS3.1, RS4.1, RS5.1, RS6.1, RUSB4.2, RUSB5.2, SERVO_CONTROLLER.14 (VSS), SERVO_CONTROLLER.25 (EXTCLK), SERVO_PINOUT.5, SERVO_PINOUT.6, SERVO_PINOUT.11, SERVO_REGULATOR.1 (GND)
LED_RS6: LED4.C@1 (C), RS6.2
OE: ROE.1, SERVO_CONTROLLER.23 (~OE)
PWM1: SERVO_CONTROLLER.6 (LED0), SERVO_PINOUT.1
PWM2: SERVO_CONTROLLER.7 (LED1), SERVO_PINOUT.7
PWM3: SERVO_CONTROLLER.8 (LED2), SERVO_PINOUT.2
SRVSCLM: D11.2 (A), I2C_USBC_OUT.A6 (DP1), I2C_USBC_OUT.B6 (DP2), SERVO_CONTROLLER.26 (SCL), SPULRSCL.2
SRVSDAM: D12.2 (A), I2C_USBC_OUT.A7 (DN1), I2C_USBC_OUT.B7 (DN2), SERVO_CONTROLLER.27 (SDA), SPULSDA.2
VBUS12: D9.A, D10.2 (A), I2C_USBC_OUT.A4-B9 (VBUS_2), I2C_USBC_OUT.A9-B4 (VBUS)

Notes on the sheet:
Servo Motors Control

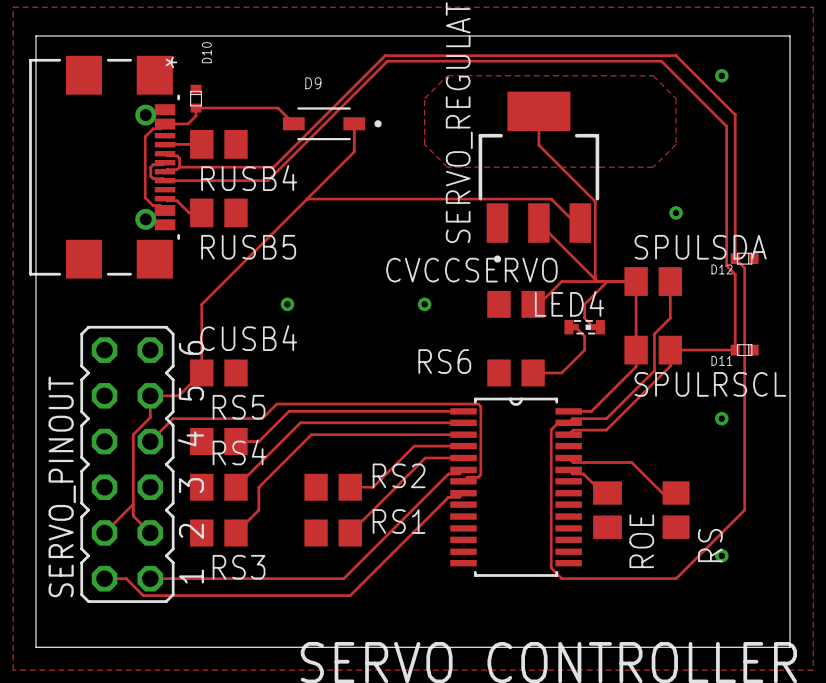
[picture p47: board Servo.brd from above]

Board: 2 copper layers, 41.9 x 34.0 mm, 23 parts (0 on the bottom side), 19 nets.

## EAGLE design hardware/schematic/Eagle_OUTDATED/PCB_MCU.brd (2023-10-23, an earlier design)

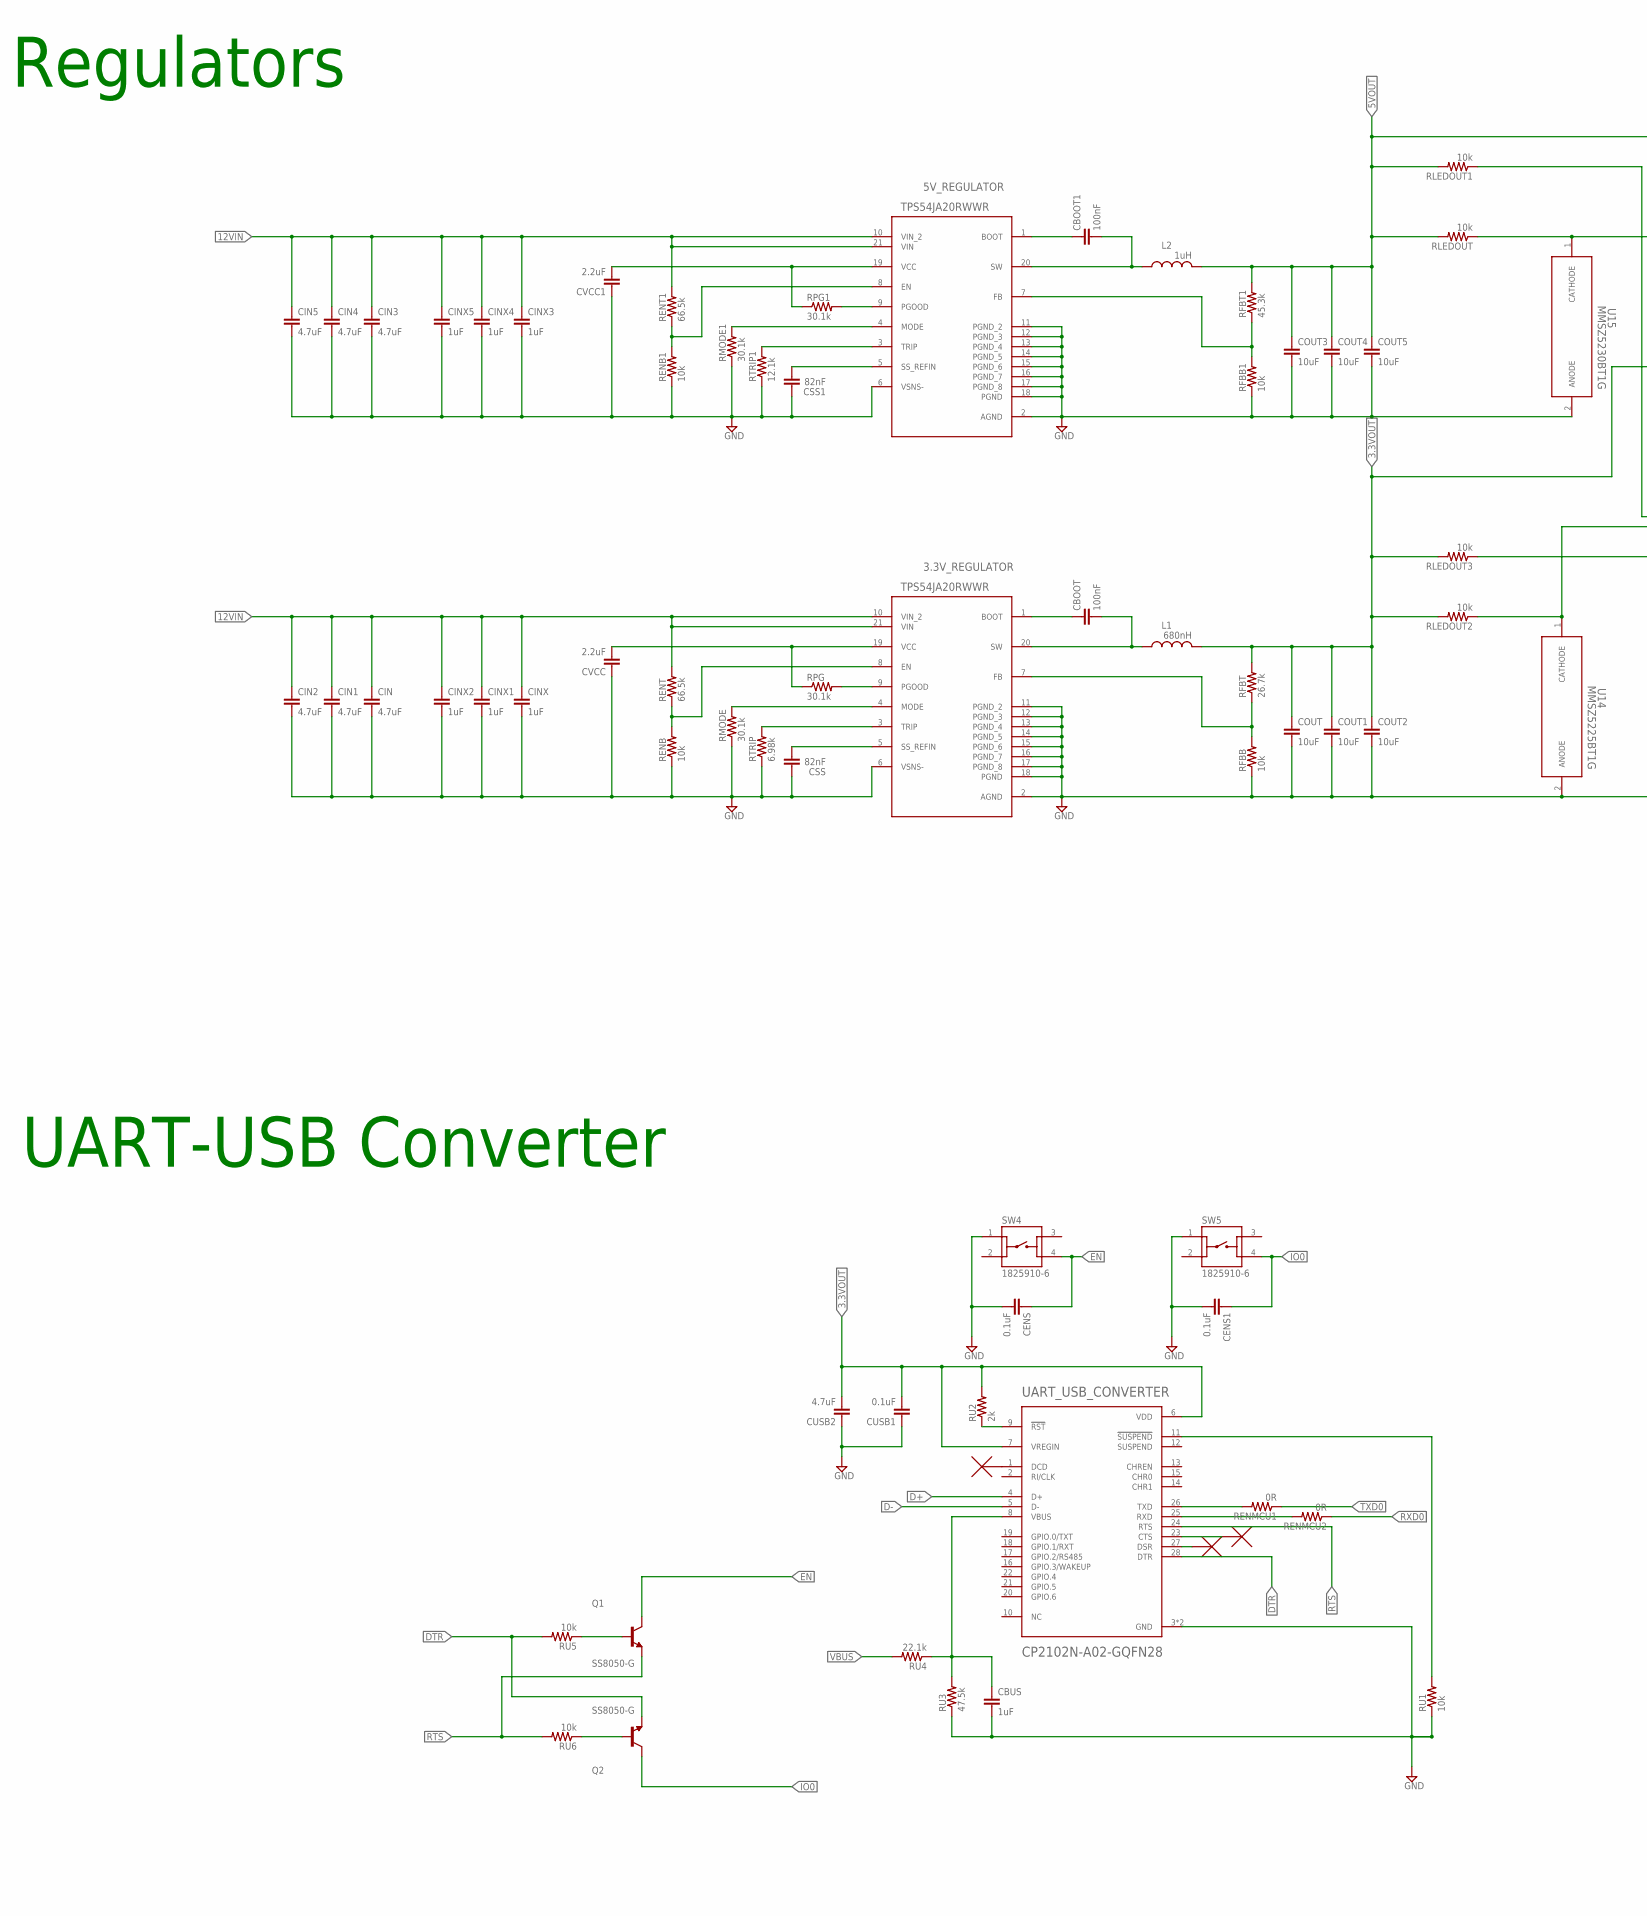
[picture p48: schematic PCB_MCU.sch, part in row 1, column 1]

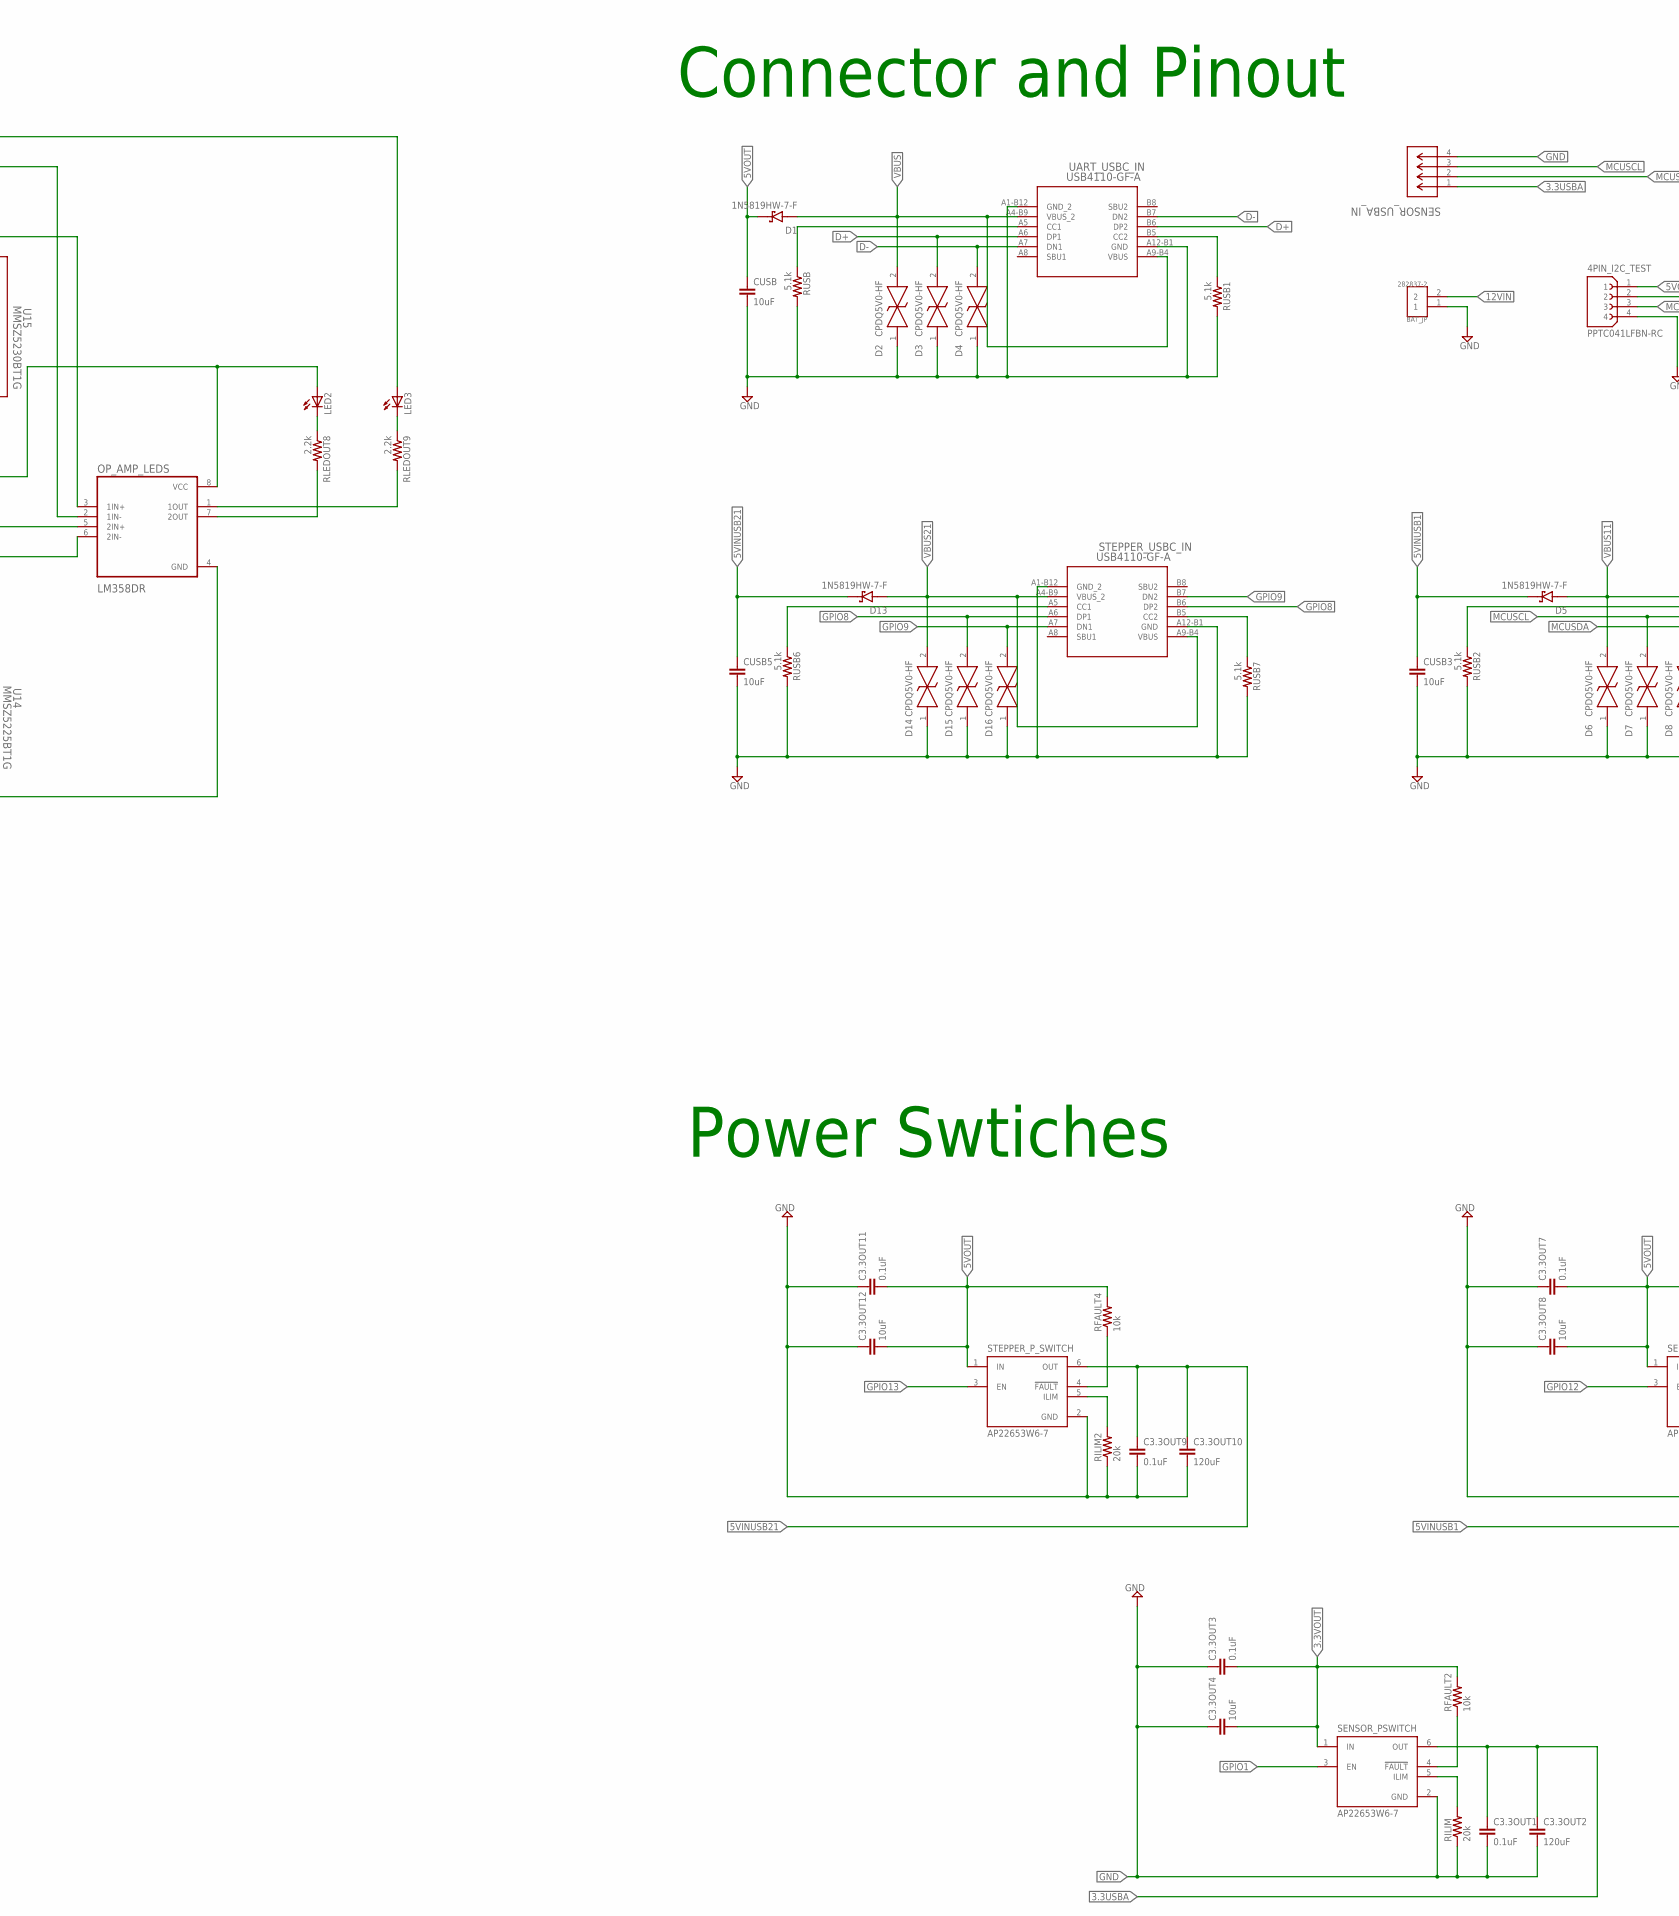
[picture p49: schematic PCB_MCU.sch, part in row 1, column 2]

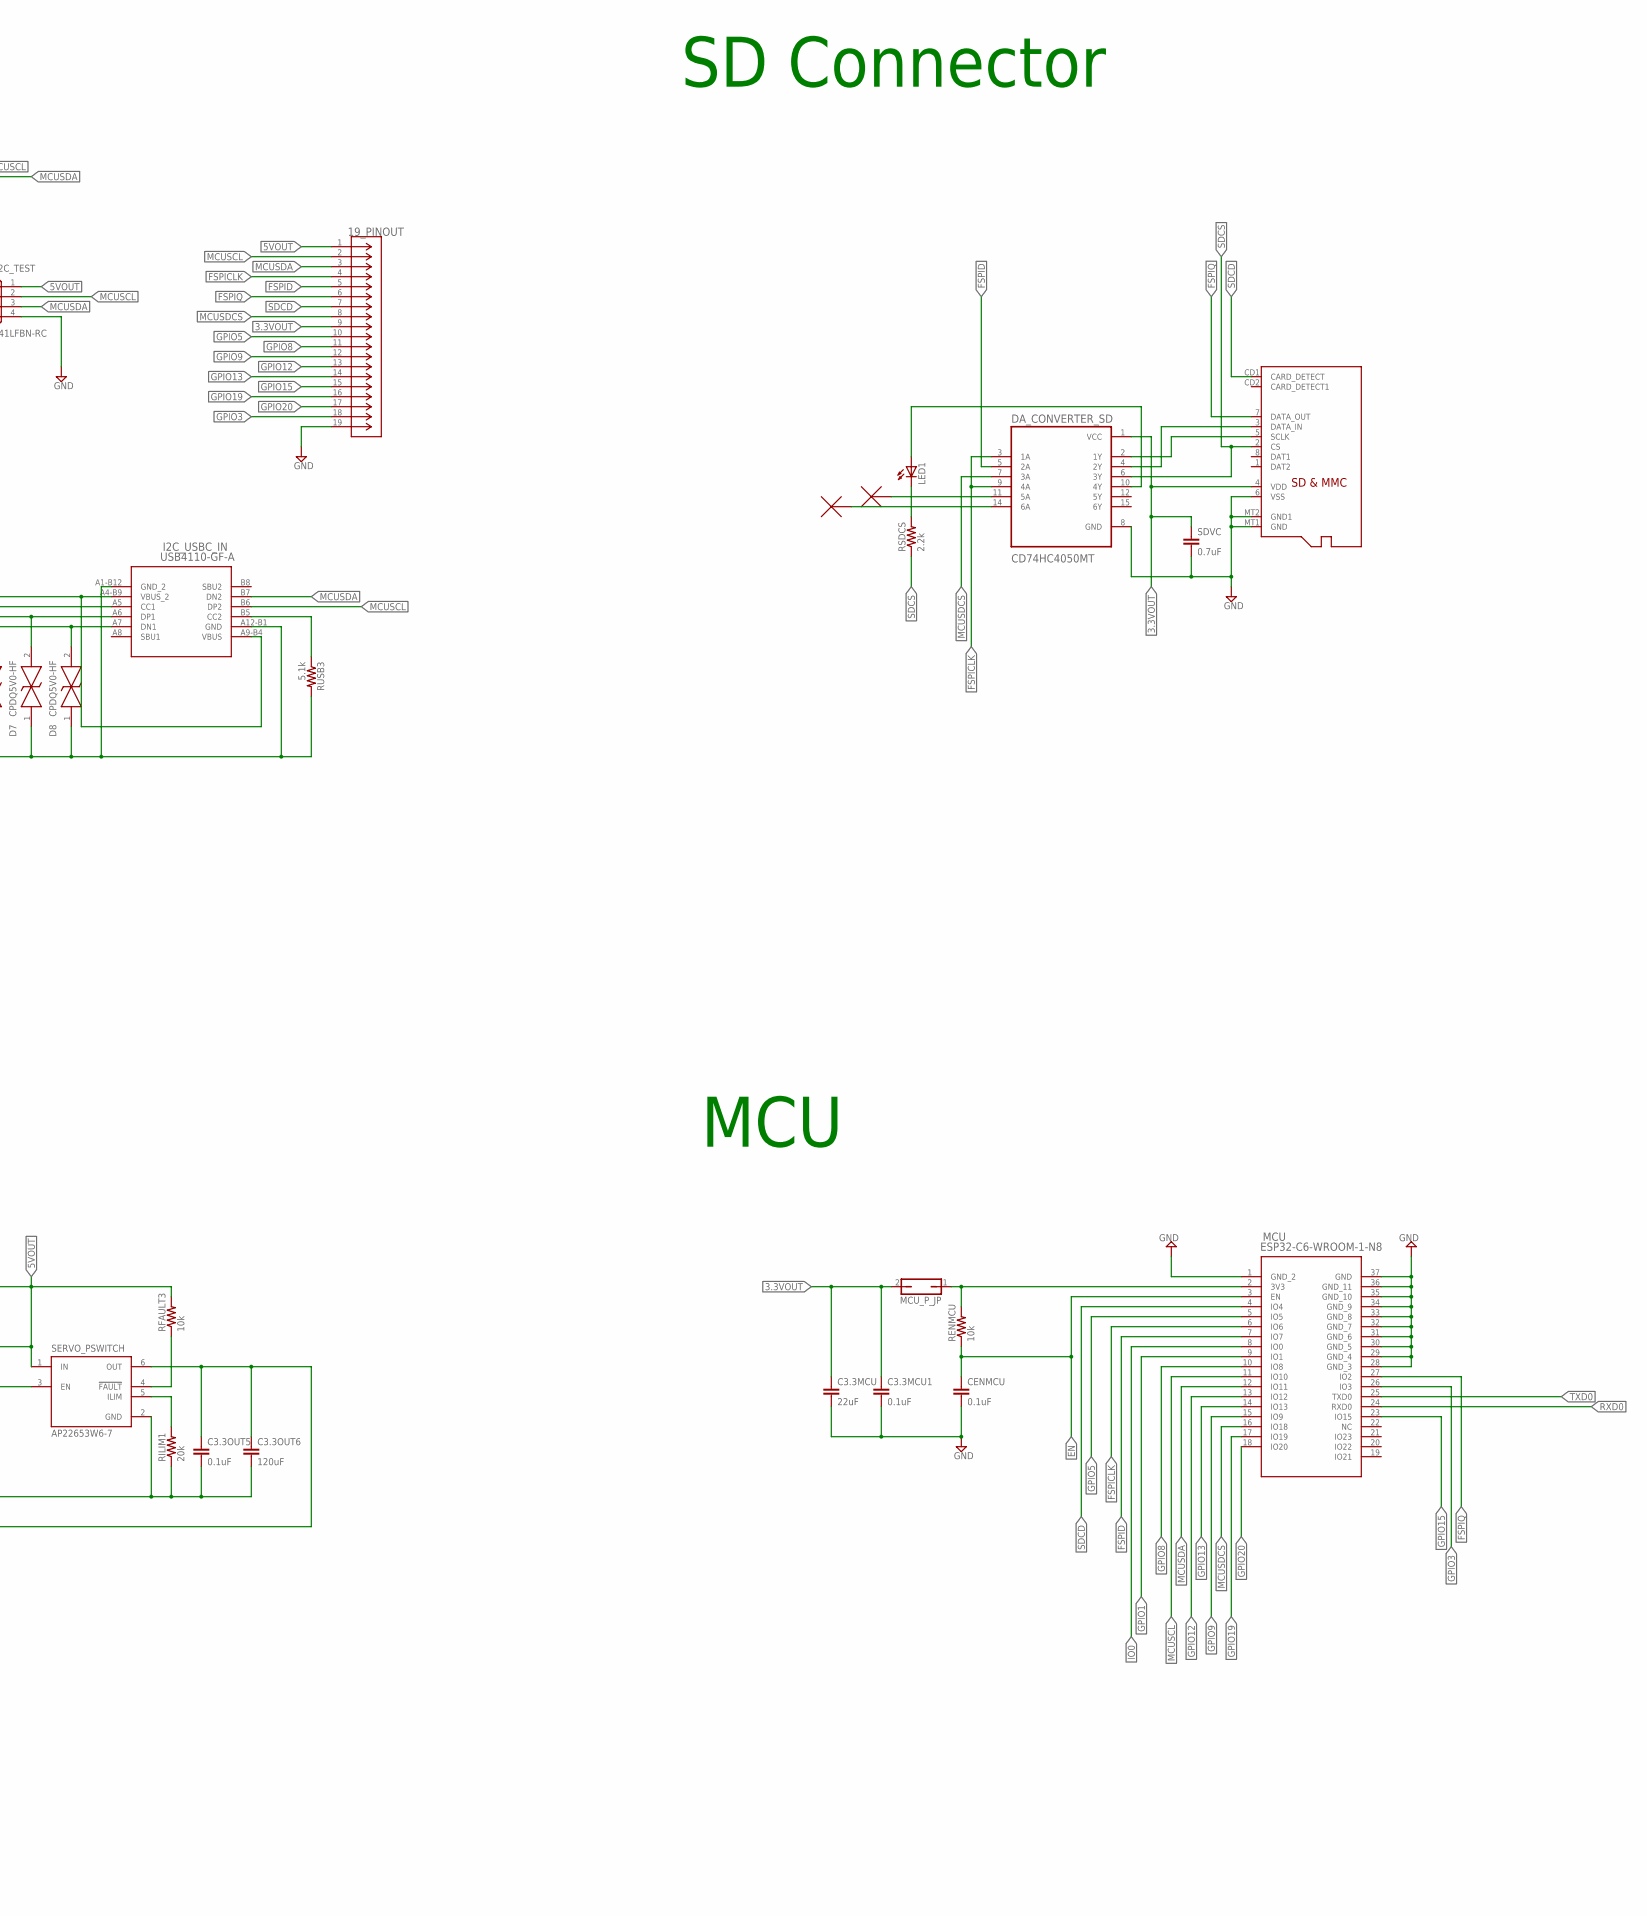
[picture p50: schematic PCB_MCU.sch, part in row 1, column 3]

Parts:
3.3V_REGULATOR, 5V_REGULATOR: TPS54JA20RWWR; RWW0021A
4PIN_I2C_TEST: PPTC041LFBN-RC; SULLINS_PPTC041LFBN-RC
19_PINOUT: PPTC191LFBN-RC; CONN19_PPTC191LFBN-RC_SUL
BAT_JP: 282837-2; TE_282837-2
C3.3MCU: 22uF; C0805
C3.3MCU1, C3.3OUT1, C3.3OUT3, C3.3OUT5, C3.3OUT7, C3.3OUT9, C3.3OUT11: 0.1uF; C0805
C3.3OUT2, C3.3OUT6, C3.3OUT10: 120uF; C0805
C3.3OUT4, C3.3OUT8, C3.3OUT12: 10uF; C0805
CBOOT, CBOOT1: 100nF; C0805
CBUS: 1uF; C0805
CENMCU: 0.1uF; C0805
CENS, CENS1: 0.1uF; C0805
CIN, CIN1, CIN2, CIN3, CIN4, CIN5: 4.7uF; C0805
CINX, CINX1, CINX2, CINX3, CINX4, CINX5: 1uF; C0805
COUT, COUT1, COUT2, COUT3, COUT4, COUT5: 10uF; C0805
CSS, CSS1: 82nF; C0805
CUSB, CUSB3, CUSB5: 10uF; C0805
CUSB1: 0.1uF; C0805
CUSB2: 4.7uF; C0805
CVCC, CVCC1: 2.2uF; C0805
D1, D5, D13: 1N5819HW-7-F; SOD3715X145N
D2, D3, D4, D6, D7, D8, D14, D15, D16: CPDQ5V0-HF; MBTB-D-SOD-923F-IMP-0402
DA_CONVERTER_SD: CD74HC4050MT; SOIC127P600X175-16N
I2C_USBC_IN: USB4110-GF-A; USB4110-GF-A_GCT
L1: 680nH; 6000-XXXX-RC
L2: 1uH; 6000-XXXX-RC
LED1, LED2, LED3: LED; SMARTLED-TTW
MCU: ESP32-C6-WROOM-1-N8; MOD28_ESP32-C6-WROOM-1_EXP
MCU_P_JP: JP1Q; JP1
OP_AMP_LEDS: LM358DR; SOIC127P599X175-8N
Q1, Q2: SS8050-G; TRANS_SS8050-G
RENB, RENB1: 10k; M0805
RENMCU: 10k; M0805
RENMCU1, RENMCU2: 0R; M0805
RENT, RENT1: 66.5k; M0805
RFAULT2, RFAULT3, RFAULT4: 10k; M0805
RFBB, RFBB1: 10k; M0805
RFBT: 26.7k; M0805
RFBT1: 45.3k; M0805
RILIM, RILIM1, RILIM2: 20k; M0805
RLEDOUT, RLEDOUT1, RLEDOUT2, RLEDOUT3: 10k; M0805
RLEDOUT8, RLEDOUT9: 2.2k; M0805
RMODE, RMODE1: 30.1k; M0805
RPG, RPG1: 30.1k; M0805
RSDCS: 2.2k; M0805
RTRIP: 6.98k; M0805
RTRIP1: 12.1k; M0805
RU1, RU5, RU6: 10k; M0805
RU2: 2k; M0805
RU3: 47.5k; M0805
RU4: 22.1k; M0805
RUSB, RUSB1, RUSB2, RUSB3, RUSB6, RUSB7: 5.1k; M0805
SDVC: 0.7uF; C0805
SD_CONNECTOR: MICROSD
SENSOR_PSWITCH: AP22653W6-7; SOT95P280X145-6N
SENSOR_USBA_IN: USB-AP-S-RA-SMT; CONN_USB-AP-S-RA-SMT_ADM
SERVO_PSWITCH: AP22653W6-7; SOT95P280X145-6N
STEPPER_P_SWITCH: AP22653W6-7; SOT95P280X145-6N
STEPPER_USBC_IN: USB4110-GF-A; USB4110-GF-A_GCT
SW4, SW5: 1825910-6; SW_1825910-6-4
U14: MMSZ5225BT1G; SOD-123_ONS
U15: MMSZ5230BT1G; SOD-123_ONS
UART_USBC_IN: USB4110-GF-A; USB4110-GF-A_GCT
UART_USB_CONVERTER: CP2102N-A02-GQFN28; QFN50P500X500X80-29N

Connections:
1I+_OP_AMP: OP_AMP_LEDS.3 (1IN+), RLEDOUT.1, U15.1 (CATHODE)
1I-_OP_AMP: OP_AMP_LEDS.2 (1IN-), RLEDOUT1.1
1O_OP_AMP: OP_AMP_LEDS.1 (1OUT), RLEDOUT9.2
2+I_OP_AMP: OP_AMP_LEDS.5 (2IN+), RLEDOUT2.1, U14.1 (CATHODE)
2-I_OP_AMP: OP_AMP_LEDS.6 (2IN-), RLEDOUT3.1
2O_OP_AMP: OP_AMP_LEDS.7 (2OUT), RLEDOUT8.2
3.3USBA: C3.3OUT1.1, C3.3OUT2.1, SENSOR_PSWITCH.6 (OUT), SENSOR_USBA_IN.1
3.3VOUT: 19_PINOUT.9, C3.3MCU.1, C3.3MCU1.1, C3.3OUT3.2, C3.3OUT4.2, COUT.1, COUT1.1, COUT2.1, CUSB1.2, CUSB2.2, DA_CONVERTER_SD.1 (VCC), L1.2, LED2.A@1 (A), MCU_P_JP.2, OP_AMP_LEDS.8 (VCC), RFAULT2.2, RFBT.2, RLEDOUT2.2, RLEDOUT3.2, RU2.2, SDVC.1, SD_CONNECTOR.4 (VDD), SENSOR_PSWITCH.1 (IN), UART_USB_CONVERTER.6 (VDD), UART_USB_CONVERTER.7 (VREGIN)
3V3_MCU: MCU.2 (3V3), MCU_P_JP.1, RENMCU.2
5ASD: DA_CONVERTER_SD.11 (5A)
5VINUSB1: C3.3OUT5.1, C3.3OUT6.1, CUSB3.1, D5.C (K), SERVO_PSWITCH.6 (OUT)
5VINUSB21: C3.3OUT9.1, C3.3OUT10.1, CUSB5.1, D13.C (K), STEPPER_P_SWITCH.6 (OUT)
5VOUT: 4PIN_I2C_TEST.1, 19_PINOUT.1, C3.3OUT7.2, C3.3OUT8.2, C3.3OUT11.2, C3.3OUT12.2, COUT3.1, COUT4.1, COUT5.1, CUSB.1, D1.C (K), L2.2, LED3.A@1 (A), RFAULT3.2, RFAULT4.2, RFBT1.2, RLEDOUT.2, RLEDOUT1.2, SERVO_PSWITCH.1 (IN), STEPPER_P_SWITCH.1 (IN)
6ASD: DA_CONVERTER_SD.14 (6A)
12VIN: 3.3V_REGULATOR.10 (VIN_2), 3.3V_REGULATOR.21 (VIN), 5V_REGULATOR.10 (VIN_2), 5V_REGULATOR.21 (VIN), BAT_JP.2, CIN.1, CIN1.1, CIN2.1, CIN3.1, CIN4.1, CIN5.1, CINX.1, CINX1.1, CINX2.1, CINX3.1, CINX4.1, CINX5.1, RENT.2, RENT1.2
BOOT_3VREG: 3.3V_REGULATOR.1 (BOOT), CBOOT.1
BOOT_5VREG: 5V_REGULATOR.1 (BOOT), CBOOT1.1
CC1_I2C: I2C_USBC_IN.A5 (CC1), RUSB2.1
CC1_STEPPER: RUSB6.1, STEPPER_USBC_IN.A5 (CC1)
CC1_UART: RUSB.1, UART_USBC_IN.A5 (CC1)
CC2_I2C: I2C_USBC_IN.B5 (CC2), RUSB3.1
CC2_STEPPER: RUSB7.1, STEPPER_USBC_IN.B5 (CC2)
CC2_UART: RUSB1.1, UART_USBC_IN.B5 (CC2)
CTS_NC: UART_USB_CONVERTER.23 (CTS)
D+: D3.2 (A), UART_USBC_IN.A6 (DP1), UART_USBC_IN.B6 (DP2), UART_USB_CONVERTER.4 (D+)
D-: D4.2 (A), UART_USBC_IN.A7 (DN1), UART_USBC_IN.B7 (DN2), UART_USB_CONVERTER.5 (D-)
DATA_I_SD: DA_CONVERTER_SD.4 (2Y), SD_CONNECTOR.3 (DATA_IN)
DSR_NC: UART_USB_CONVERTER.27 (DSR)
DTR: Q2.2 (E), RU5.2, UART_USB_CONVERTER.28 (DTR)
EN: CENMCU.1, CENS.1, MCU.3 (EN), Q1.3 (C), RENMCU.1, SW4.4
EN_3VREG: 3.3V_REGULATOR.8 (EN), RENB.2, RENT.1
EN_5VREG: 5V_REGULATOR.8 (EN), RENB1.2, RENT1.1
FAULT_SENSOR_S: RFAULT2.1, SENSOR_PSWITCH.4 (!FAULT)
FAULT_SERVO_S: RFAULT3.1, SERVO_PSWITCH.4 (!FAULT)
FAULT_STEPPER_S: RFAULT4.1, STEPPER_P_SWITCH.4 (!FAULT)
FB_3VREG: 3.3V_REGULATOR.7 (FB), RFBB.2, RFBT.1
FB_5VREG: 5V_REGULATOR.7 (FB), RFBB1.2, RFBT1.1
FSPICLK: 19_PINOUT.4, DA_CONVERTER_SD.3 (1A), DA_CONVERTER_SD.9 (4A), MCU.6 (IO6)
FSPID: 19_PINOUT.5, DA_CONVERTER_SD.5 (2A), MCU.7 (IO7)
FSPIQ: 19_PINOUT.6, MCU.27 (IO2), SD_CONNECTOR.7 (DATA_OUT)
GND: 3.3V_REGULATOR.2 (AGND), 3.3V_REGULATOR.6 (VSNS-), 3.3V_REGULATOR.11 (PGND_2), 3.3V_REGULATOR.12 (PGND_3), 3.3V_REGULATOR.13 (PGND_4), 3.3V_REGULATOR.14 (PGND_5), 3.3V_REGULATOR.15 (PGND_6), 3.3V_REGULATOR.16 (PGND_7), 3.3V_REGULATOR.17 (PGND_8), 3.3V_REGULATOR.18 (PGND), 4PIN_I2C_TEST.4, 5V_REGULATOR.2 (AGND), 5V_REGULATOR.6 (VSNS-), 5V_REGULATOR.11 (PGND_2), 5V_REGULATOR.12 (PGND_3), 5V_REGULATOR.13 (PGND_4), 5V_REGULATOR.14 (PGND_5), 5V_REGULATOR.15 (PGND_6), 5V_REGULATOR.16 (PGND_7), 5V_REGULATOR.17 (PGND_8), 5V_REGULATOR.18 (PGND), 19_PINOUT.19, BAT_JP.1, C3.3MCU.2, C3.3MCU1.2, C3.3OUT1.2, C3.3OUT2.2, C3.3OUT3.1, C3.3OUT4.1, C3.3OUT5.2, C3.3OUT6.2, C3.3OUT7.1, C3.3OUT8.1, C3.3OUT9.2, C3.3OUT10.2, C3.3OUT11.1, C3.3OUT12.1, CBUS.2, CENMCU.2, CENS.2, CENS1.2, CIN.2, CIN1.2, CIN2.2, CIN3.2, CIN4.2, CIN5.2, CINX.2, CINX1.2, CINX2.2, CINX3.2, CINX4.2, CINX5.2, COUT.2, COUT1.2, COUT2.2, COUT3.2, COUT4.2, COUT5.2, CSS.1, CSS1.1, CUSB.2, CUSB1.1, CUSB2.1, CUSB3.2, CUSB5.2, CVCC.1, CVCC1.1, D2.1 (K), D3.1 (K), D4.1 (K), D6.1 (K), D7.1 (K), D8.1 (K), D14.1 (K), D15.1 (K), D16.1 (K), DA_CONVERTER_SD.8 (GND), I2C_USBC_IN.A1-B12 (GND_2), I2C_USBC_IN.A12-B1 (GND), MCU.1 (GND_2), MCU.28 (GND_3), MCU.29 (GND_4), MCU.30 (GND_5), MCU.31 (GND_6), MCU.32 (GND_7), MCU.33 (GND_8), MCU.34 (GND_9), MCU.35 (GND_10), MCU.36 (GND_11), MCU.37 (GND), OP_AMP_LEDS.4 (GND), RENB.1, RENB1.1, RFBB.1, RFBB1.1, RILIM.1, RILIM1.1, RILIM2.1, RMODE.1, RMODE1.1, RTRIP.1, RTRIP1.1, RU1.1, RU3.1, RUSB.2, RUSB1.2, RUSB2.2, RUSB3.2, RUSB6.2, RUSB7.2, SDVC.2, SD_CONNECTOR.6 (VSS), SD_CONNECTOR.MT1 (GND), SD_CONNECTOR.MT2 (GND1), SENSOR_PSWITCH.2 (GND), SENSOR_USBA_IN.4, SERVO_PSWITCH.2 (GND), STEPPER_P_SWITCH.2 (GND), STEPPER_USBC_IN.A1-B12 (GND_2), STEPPER_USBC_IN.A12-B1 (GND), SW4.1, SW5.1, U14.2 (ANODE), U15.2 (ANODE), UART_USBC_IN.A1-B12 (GND_2), UART_USBC_IN.A12-B1 (GND), UART_USB_CONVERTER.3 (GND), UART_USB_CONVERTER.29 (GND)
GPIO1: MCU.9 (IO1), SENSOR_PSWITCH.3 (EN)
GPIO3: 19_PINOUT.18, MCU.26 (IO3)
GPIO5: 19_PINOUT.10, MCU.5 (IO5)
GPIO8: 19_PINOUT.11, D15.2 (A), MCU.10 (IO8), STEPPER_USBC_IN.A6 (DP1), STEPPER_USBC_IN.B6 (DP2)
GPIO9: 19_PINOUT.12, D16.2 (A), MCU.15 (IO9), STEPPER_USBC_IN.A7 (DN1), STEPPER_USBC_IN.B7 (DN2)
GPIO12: 19_PINOUT.13, MCU.13 (IO12), SERVO_PSWITCH.3 (EN)
GPIO13: 19_PINOUT.14, MCU.14 (IO13), STEPPER_P_SWITCH.3 (EN)
GPIO15: 19_PINOUT.15, MCU.23 (IO15)
GPIO19: 19_PINOUT.16, MCU.17 (IO19)
GPIO20: 19_PINOUT.17, MCU.18 (IO20)
ILIM_SENSOR_S: RILIM.2, SENSOR_PSWITCH.5 (ILIM)
ILIM_SERVO_S: RILIM1.2, SERVO_PSWITCH.5 (ILIM)
ILIM_STEPPER_S: RILIM2.2, STEPPER_P_SWITCH.5 (ILIM)
IO0: CENS1.1, MCU.8 (IO0), Q2.3 (C), SW5.4
LED1_RSDCS: LED1.C@1 (C), RSDCS.2
LED2_RLED8: LED2.C@1 (C), RLEDOUT8.1
LED3_RLED9: LED3.C@1 (C), RLEDOUT9.1
LED_CONVERTER: DA_CONVERTER_SD.10 (4Y), LED1.A@1 (A)
MCUSCL: 4PIN_I2C_TEST.2, 19_PINOUT.2, D7.2 (A), I2C_USBC_IN.A6 (DP1), I2C_USBC_IN.B6 (DP2), MCU.11 (IO10), SENSOR_USBA_IN.3
MCUSDA: 4PIN_I2C_TEST.3, 19_PINOUT.3, D8.2 (A), I2C_USBC_IN.A7 (DN1), I2C_USBC_IN.B7 (DN2), MCU.12 (IO11), SENSOR_USBA_IN.2
MCUSDCS: 19_PINOUT.8, DA_CONVERTER_SD.7 (3A), MCU.16 (IO18)
MODE_3VREG: 3.3V_REGULATOR.4 (MODE), RMODE.2
MODE_5VREG: 5V_REGULATOR.4 (MODE), RMODE1.2
unnamed: Q1.1 (B), RU5.1
unnamed: Q2.1 (B), RU6.1
PGOOD_3VREG: 3.3V_REGULATOR.9 (PGOOD), RPG.2
PGOOD_5VREG: 5V_REGULATOR.9 (PGOOD), RPG1.2
RST_UART_CONV: RU2.1, UART_USB_CONVERTER.9 (!RST)
RTS: Q1.2 (E), RU6.2, UART_USB_CONVERTER.24 (RTS)
RXD0: MCU.24 (RXD0), RENMCU2.1
RXD_UART_CONV: RENMCU2.2, UART_USB_CONVERTER.25 (RXD)
SDCD: 19_PINOUT.7, MCU.4 (IO4), SD_CONNECTOR.CD1 (CARD_DETECT)
SDCS: DA_CONVERTER_SD.6 (3Y), RSDCS.1, SD_CONNECTOR.2 (CS)
SD_CLK: DA_CONVERTER_SD.2 (1Y), SD_CONNECTOR.5 (SCLK)
SS_REFIN_3VREG: 3.3V_REGULATOR.5 (SS_REFIN), CSS.2
SS_REFIN_5VREG: 5V_REGULATOR.5 (SS_REFIN), CSS1.2
SUSPEND: RU1.2, UART_USB_CONVERTER.11 (!SUSPEND)
SW_3VREG: 3.3V_REGULATOR.20 (SW), CBOOT.2, L1.1
SW_5VREG: 5V_REGULATOR.20 (SW), CBOOT1.2, L2.1
TRIP_3VREG: 3.3V_REGULATOR.3 (TRIP), RTRIP.2
TRIP_5VREG: 5V_REGULATOR.3 (TRIP), RTRIP1.2
TXD0: MCU.25 (TXD0), RENMCU1.1
TXD_UART_CONV: RENMCU1.2, UART_USB_CONVERTER.26 (TXD)
VBUS: D1.A, D2.2 (A), RU4.2, UART_USBC_IN.A4-B9 (VBUS_2), UART_USBC_IN.A9-B4 (VBUS)
VBUS11: D5.A, D6.2 (A), I2C_USBC_IN.A4-B9 (VBUS_2), I2C_USBC_IN.A9-B4 (VBUS)
VBUS21: D13.A, D14.2 (A), STEPPER_USBC_IN.A4-B9 (VBUS_2), STEPPER_USBC_IN.A9-B4 (VBUS)
VBUS_UART_CONV: CBUS.1, RU3.2, RU4.1, UART_USB_CONVERTER.8 (VBUS)
VCC_3VREG: 3.3V_REGULATOR.19 (VCC), CVCC.2, RPG.1
VCC_5VREG: 5V_REGULATOR.19 (VCC), CVCC1.2, RPG1.1

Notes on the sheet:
Regulators
UART-USB Converter
Power Swtiches
Connector and Pinout
SD Connector
MCU

Board: 2 copper layers, 131 parts (0 on the bottom side), 86 nets, no tracks yet.

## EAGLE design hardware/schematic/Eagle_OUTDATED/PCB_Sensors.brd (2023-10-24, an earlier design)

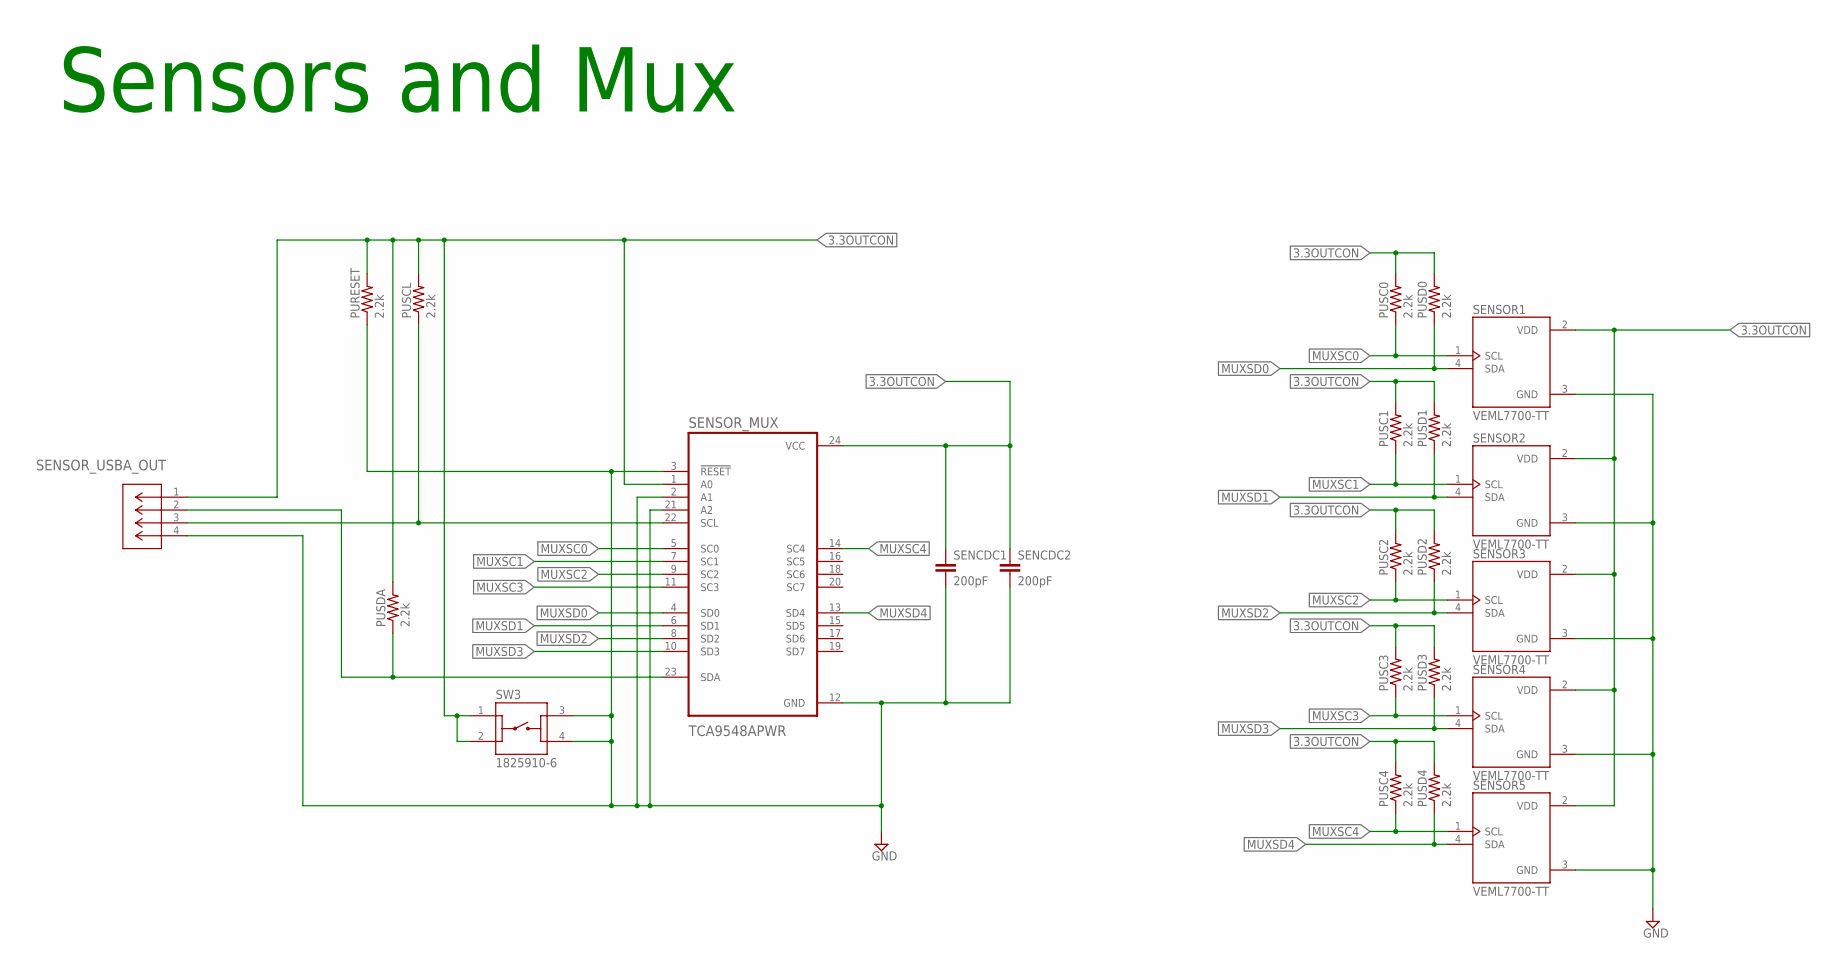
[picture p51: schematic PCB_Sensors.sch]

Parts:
PURESET: 2.2k; M0805
PUSC0, PUSC1, PUSC2, PUSC3, PUSC4: 2.2k; M0805
PUSCL: 2.2k; M0805
PUSD0, PUSD1, PUSD2, PUSD3, PUSD4: 2.2k; M0805
PUSDA: 2.2k; M0805
SENCDC1, SENCDC2: 200pF; C0805
SENSOR1, SENSOR2, SENSOR3, SENSOR4, SENSOR5: VEML7700-TT; XDCR_VEML7700-TT
SENSOR_MUX: TCA9548APWR; SOP65P640X120-24N
SENSOR_USBA_OUT: USB-AP-S-RA-SMT; CONN_USB-AP-S-RA-SMT_ADM
SW3: 1825910-6; SW_1825910-6-4

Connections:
3.3OUTCON: PURESET.2, PUSC0.2, PUSC1.2, PUSC2.2, PUSC3.2, PUSC4.2, PUSCL.2, PUSD0.2, PUSD1.2, PUSD2.2, PUSD3.2, PUSD4.2, PUSDA.2, SENCDC1.1, SENCDC2.1, SENSOR1.2 (VDD), SENSOR2.2 (VDD), SENSOR3.2 (VDD), SENSOR4.2 (VDD), SENSOR5.2 (VDD), SENSOR_MUX.1 (A0), SENSOR_MUX.24 (VCC), SENSOR_USBA_OUT.1, SW3.1, SW3.2
GND: PURESET.1, SENCDC1.2, SENCDC2.2, SENSOR1.3 (GND), SENSOR2.3 (GND), SENSOR3.3 (GND), SENSOR4.3 (GND), SENSOR5.3 (GND), SENSOR_MUX.2 (A1), SENSOR_MUX.3 (!RESET), SENSOR_MUX.12 (GND), SENSOR_MUX.21 (A2), SENSOR_USBA_OUT.4, SW3.3, SW3.4
MCUI2CSCL: PUSCL.1, SENSOR_MUX.22 (SCL), SENSOR_USBA_OUT.3
MCUI2CSDA: PUSDA.1, SENSOR_MUX.23 (SDA), SENSOR_USBA_OUT.2
MUXSC0: PUSC0.1, SENSOR1.1 (SCL), SENSOR_MUX.5 (SC0)
MUXSC1: PUSC1.1, SENSOR2.1 (SCL), SENSOR_MUX.7 (SC1)
MUXSC2: PUSC2.1, SENSOR3.1 (SCL), SENSOR_MUX.9 (SC2)
MUXSC3: PUSC3.1, SENSOR4.1 (SCL), SENSOR_MUX.11 (SC3)
MUXSC4: PUSC4.1, SENSOR5.1 (SCL), SENSOR_MUX.14 (SC4)
MUXSD0: PUSD0.1, SENSOR1.4 (SDA), SENSOR_MUX.4 (SD0)
MUXSD1: PUSD1.1, SENSOR2.4 (SDA), SENSOR_MUX.6 (SD1)
MUXSD2: PUSD2.1, SENSOR3.4 (SDA), SENSOR_MUX.8 (SD2)
MUXSD3: PUSD3.1, SENSOR4.4 (SDA), SENSOR_MUX.10 (SD3)
MUXSD4: PUSD4.1, SENSOR5.4 (SDA), SENSOR_MUX.13 (SD4)

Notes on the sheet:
Sensors and Mux

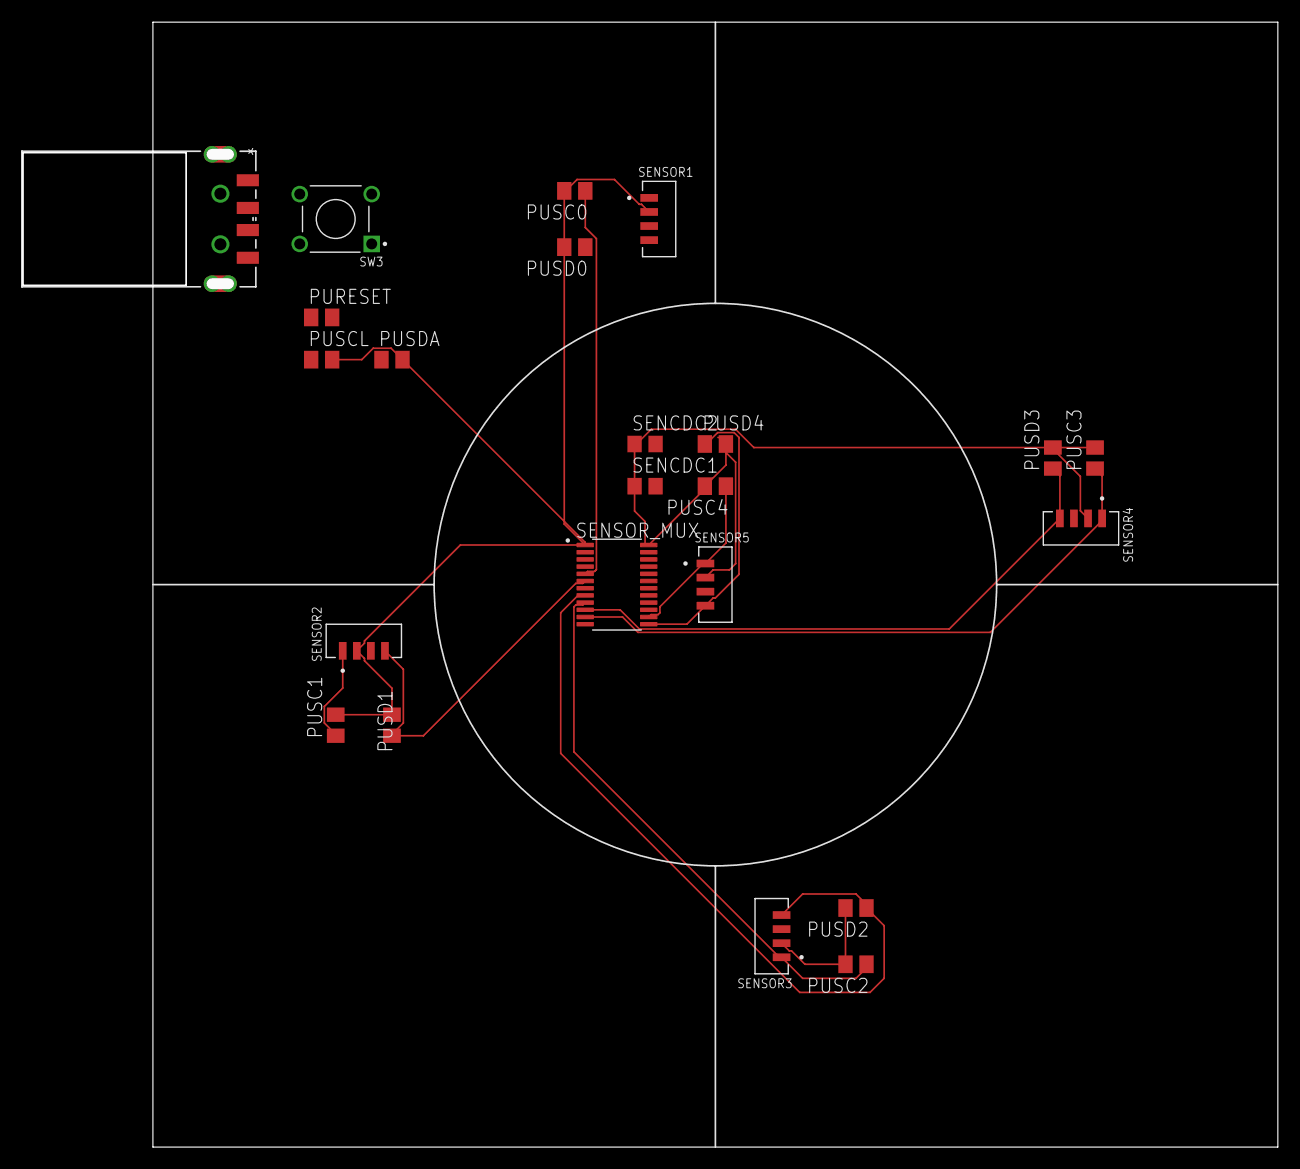
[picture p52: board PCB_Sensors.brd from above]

Board: 2 copper layers, 101.6 x 101.6 mm, 23 parts (0 on the bottom side), 14 nets.

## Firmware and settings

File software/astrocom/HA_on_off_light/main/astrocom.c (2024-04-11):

// YOU NEED TO DISABLE WATCHDOG TIMER IN MENUCONFIG TO RUN THIS CODE
// Component config -> ESP System settings -> Disable Task Watchdog Timer

// includes Vishay VEML7700 Light Sensor driver for integration with ESP-IDF framework by Kristijan Grozdanovski
// Copyright (c) 2022, Kristijan Grozdanovski

#include <stdio.h>
#include <math.h>
#include "driver/i2c.h"
#include "veml7700.h"
#include "esp_log.h"
#include "driver/gpio.h"
#include "esp_intr_alloc.h"
#include "esp_timer.h"
// zigbee libraries
#include "freertos/FreeRTOS.h"
#include "freertos/task.h"
#include "managed_components/espressif__esp-zigbee-lib/include/ha/esp_zigbee_ha_standard.h"
#include "managed_components/espressif__esp-zigbee-lib/include/esp_zb_light.h"
#include "nvs_flash.h"

#define I2C_MASTER_SCL_IO 10            // GPIO for sensor I2C clock
#define I2C_MASTER_SDA_IO 11            // GPIO for sensor I2C data
#define I2C_MASTER_NUM I2C_NUM_0
#define TCA9548_ADDR 0x71
//-----------------------------------------------------------------------------------------
#define USBC_PIN GPIO_NUM_12 // Define GPIO pin 12
#define USBA_PIN GPIO_NUM_1 // Define GPIO pin 1
#define STEP_PIN GPIO_NUM_22        // CLK pin 22
#define DIR_PIN GPIO_NUM_23         // DIR pin 23

// PCA9685 I2C address
#define PCA9685_ADDR    0x40

// Registers
#define PCA9685_MODE1   0x00
#define PCA9685_PRESCALE 0xFE
#define LED0_ON_L       0x06
#define LED0_ON_H       0x07
#define LED0_OFF_L      0x08
#define LED0_OFF_H      0x09

#define SERVO_NUM       3

// I2C Configuration
#define I2C_PORT        0
#define I2C_FREQ_HZ     50000 // 20kHz

// Configuration for servo motors
#define SERVO_FREQ_HZ   50
#define SERVO_MIN_US    500
#define SERVO_MAX_US    2500
#define SERVO_MIN_AN    90
#define SERVO_MAX_AN    360

// global variables to store sensor and mirror values
float angle_spin = 0.0;
float save_value = 0.0;
float angle_val = 0.0;
float new_mirror_vert = 0.0;
float new_mirror_horiz = 0.0;

int target_num = 0; // target number
int dir = 1; // direction of stepper
int target_change_var = 0; // boolean that ignores thresholds when changing targets

// global variables to store stepper values
float current_stepper_val = 0.0;
float stepper_save_value = 0.0;
float stepper_val_new = 0.0;

// target location arrays
float target_val_servo[] = {600,450};
float target_val_stepper[] = {0,720};

// function prototype for slow servo spin
void set_servo_angle_loop(float new_value, float current_value, int channel);

//-------------------------ZIGBEE------------------------------------
/**
 * @note Make sure set idf.py menuconfig in zigbee component as zigbee end device!
*/
#if !defined ZB_ED_ROLE
#error Define ZB_ED_ROLE in idf.py menuconfig to compile light (End Device) source code.
#endif

// manufacturer info
char modelid[] = {11, 'E', 'S', 'P', '3', '2', 'C', '6', '.', 'E', 'n', 'd'};
char manufname[] = {9, 'E', 's', 'p', 'r', 'e', 's', 's', 'i', 'f'};

static const char *TAG = "ASTROCOM";
/********************* Define functions **************************/
static void bdb_start_top_level_commissioning_cb(uint8_t mode_mask)
{
    ESP_ERROR_CHECK(esp_zb_bdb_start_top_level_commissioning(mode_mask));
}

void attr_cb(uint8_t status, uint8_t endpoint, uint16_t cluster_id, uint16_t attr_id, void *new_value)
{
    if (cluster_id == ESP_ZB_ZCL_CLUSTER_ID_ON_OFF) {
        uint8_t value = *(uint8_t *)new_value;
        if (attr_id == ESP_ZB_ZCL_ATTR_ON_OFF_ON_OFF_ID) {
            /* implemented light on/off control */
            if (!target_num)
            {
                target_change_var++;
                target_num++;
                ESP_LOGI(TAG, "set to target 1");
                gpio_set_level(20, 1);
            }
            else if (target_num)
            {
                new_mirror_horiz -= 20;
                target_change_var++;
                target_num--;
                ESP_LOGI(TAG, "set to target 0");
                gpio_set_level(20, 0);
            }
            light_driver_set_power((bool)value);
        }
    } else {
        /* Implement some actions if needed when other cluster changed */
        ESP_LOGI(TAG, "cluster:0x%x, attribute:0x%x changed ", cluster_id, attr_id);
    }
}

void esp_zb_app_signal_handler(esp_zb_app_signal_t *signal_struct)
{
    uint32_t *p_sg_p       = signal_struct->p_app_signal;
    esp_err_t err_status = signal_struct->esp_err_status;
    esp_zb_app_signal_type_t sig_type = *p_sg_p;
    switch (sig_type) {
    case ESP_ZB_ZDO_SIGNAL_SKIP_STARTUP:
        ESP_LOGI(TAG, "Zigbee stack initialized");
        esp_zb_bdb_start_top_level_commissioning(ESP_ZB_BDB_MODE_INITIALIZATION);
        break;
    case ESP_ZB_BDB_SIGNAL_DEVICE_FIRST_START:
    case ESP_ZB_BDB_SIGNAL_DEVICE_REBOOT:
        if (err_status == ESP_OK) {
            ESP_LOGI(TAG, "Start network steering");
            esp_zb_bdb_start_top_level_commissioning(ESP_ZB_BDB_MODE_NETWORK_STEERING);
        } else {
            /* commissioning failed */
            ESP_LOGW(TAG, "Failed to initialize Zigbee stack (status: %d)", err_status);
        }
        break;
    case ESP_ZB_BDB_SIGNAL_STEERING:
        if (err_status == ESP_OK) {
            esp_zb_ieee_addr_t extended_pan_id;
            esp_zb_get_extended_pan_id(extended_pan_id);
            ESP_LOGI(TAG, "Joined network successfully (Extended PAN ID: %02x:%02x:%02x:%02x:%02x:%02x:%02x:%02x, PAN ID: 0x%04hx, Channel:%d)",
                     extended_pan_id[7], extended_pan_id[6], extended_pan_id[5], extended_pan_id[4],
                     extended_pan_id[3], extended_pan_id[2], extended_pan_id[1], extended_pan_id[0],
                     esp_zb_get_pan_id(), esp_zb_get_current_channel());
        } else {
            ESP_LOGI(TAG, "Network steering was not successful (status: %d)", err_status);
            esp_zb_scheduler_alarm((esp_zb_callback_t)bdb_start_top_level_commissioning_cb, ESP_ZB_BDB_MODE_NETWORK_STEERING, 1000);
        }
        break;
    default:
        ESP_LOGI(TAG, "ZDO signal: %d, status: %d", sig_type, err_status);
        break;
    }
}

static void esp_zb_task(void *pvParameters)
{
    /* initialize Zigbee stack with Zigbee end-device config */
    esp_zb_cfg_t zb_nwk_cfg = ESP_ZB_ZED_CONFIG();
    esp_zb_init(&zb_nwk_cfg);
    /* set the on-off light device config */
    esp_zb_on_off_light_cfg_t light_cfg = ESP_ZB_DEFAULT_ON_OFF_LIGHT_CONFIG();
    esp_zb_ep_list_t *esp_zb_on_off_light_ep = esp_zb_on_off_light_ep_create(HA_ESP_LIGHT_ENDPOINT, &light_cfg);
    // make cluster + send info
    esp_zb_attribute_list_t *esp_zb_basic_cluster = esp_zb_zcl_attr_list_create(ESP_ZB_ZCL_CLUSTER_ID_BASIC);
    esp_zb_basic_cluster_add_attr(esp_zb_basic_cluster, ESP_ZB_ZCL_ATTR_BASIC_MODEL_IDENTIFIER_ID, &modelid[0]);
    esp_zb_basic_cluster_add_attr(esp_zb_basic_cluster, ESP_ZB_ZCL_ATTR_BASIC_MANUFACTURER_NAME_ID, &manufname[0]);
    //
    esp_zb_device_register(esp_zb_on_off_light_ep);
    esp_zb_device_add_set_attr_value_cb(attr_cb);
    esp_zb_set_primary_network_channel_set(ESP_ZB_PRIMARY_CHANNEL_MASK);
    ESP_ERROR_CHECK(esp_zb_start(false));
    esp_zb_main_loop_iteration();
}
//------------------------------END OF ZIGBEE---------------------------------------------------

//------------------------------SERVO MUX FUNCTIONS---------------------------------------------
void pca9685_write_byte(i2c_port_t i2c_num, uint8_t reg_addr, uint8_t data) {
    i2c_cmd_handle_t cmd = i2c_cmd_link_create();
    i2c_master_start(cmd);
    i2c_master_write_byte(cmd, (PCA9685_ADDR << 1) | I2C_MASTER_WRITE, true);
    i2c_master_write_byte(cmd, reg_addr, true);
    i2c_master_write_byte(cmd, data, true);
    i2c_master_stop(cmd);
    i2c_master_cmd_begin(i2c_num, cmd, pdMS_TO_TICKS(1000));
    i2c_cmd_link_delete(cmd);
}

void pca9685_set_pwm(i2c_port_t i2c_num, uint8_t channel, uint16_t on_time, uint16_t off_time) {
    uint8_t reg_addr = LED0_ON_L + 4 * channel;
    uint8_t on_l = on_time & 0xFF;
    uint8_t on_h = (on_time >> 8) & 0x0F;
    uint8_t off_l = off_time & 0xFF;
    uint8_t off_h = (off_time >> 8) & 0x0F;

    pca9685_write_byte(i2c_num, reg_addr, on_l);
    pca9685_write_byte(i2c_num, reg_addr + 1, on_h);
    pca9685_write_byte(i2c_num, reg_addr + 2, off_l);   
    pca9685_write_byte(i2c_num, reg_addr + 3, off_h);

}

void pca9685_init(i2c_port_t i2c_num) {
    pca9685_write_byte(i2c_num, PCA9685_MODE1, 0x00); // Reset PCA9685

    // Set PWM frequency
    uint8_t prescale_val = (uint8_t)(25000000 / (4096 * SERVO_FREQ_HZ) - 1);
    pca9685_write_byte(i2c_num, PCA9685_PRESCALE, prescale_val);

    // Restart PCA9685
    pca9685_write_byte(i2c_num, PCA9685_MODE1, 0xA1);
    vTaskDelay(pdMS_TO_TICKS(5)); // Delay at least 500us after restart

    // Set all channels off initially
    for (int i = 0; i < SERVO_NUM; i++) {
        pca9685_set_pwm(i2c_num, i, 0, 0);
    }
}
//-----------------------END OF SERVO MUX FUNCTIONS---------------------------------------------

//------------------------------SERVO CTL FUNCTIONS---------------------------------------------
void set_servo_angle(i2c_port_t i2c_num, uint8_t channel, double angle) {
    // Calculate pulse length
    uint16_t pulse = (uint16_t)(SERVO_MIN_US + (angle / 180.0) * (SERVO_MAX_US - SERVO_MIN_US));
    uint16_t pwm_val = (uint16_t)(pulse * 4096 / 20000); // 20ms (50Hz) period for servos

    // Set PWM for the servo channel
    pca9685_set_pwm(i2c_num, channel, 0, pwm_val);
}

void set_servo_angle_loop(float new_value, float current_value, int channel)
{
    if(new_value < current_value)
    {
        for(int i=current_value; i>=new_value; i--){
            set_servo_angle(I2C_PORT, channel, i);
            vTaskDelay(pdMS_TO_TICKS(30));
        }
    }
    else if(new_value > current_value)
    {
        for(int i=current_value; i<=new_value; i++){
            set_servo_angle(I2C_PORT, channel, i);
            vTaskDelay(pdMS_TO_TICKS(30));
        }
    } 
}
//------------------------END OF SERVO CTL FUNCTIONS---------------------------------------------

//-------------------------------------------------------------------------------
// timer interrupt handler prototype
void timer_isr(void* arg);

// structure of light sensor
typedef struct {
    veml7700_handle_t dev;
    double lux;
    double fc;
} VEML_Data;

// I2C init function
void i2c_master_init() {
    i2c_config_t conf;
    conf.mode = I2C_MODE_MASTER;
    conf.sda_io_num = I2C_MASTER_SDA_IO;
    conf.sda_pullup_en = GPIO_PULLUP_ENABLE;
    conf.scl_io_num = I2C_MASTER_SCL_IO;
    conf.scl_pullup_en = GPIO_PULLUP_ENABLE;
    conf.master.clk_speed = I2C_FREQ_HZ; // 100 kHz clock speed
    conf.clk_flags = 0;
    i2c_param_config(I2C_MASTER_NUM, &conf);
    i2c_driver_install(I2C_MASTER_NUM, conf.mode, 0, 0, 0);
}

// sensor mux channel select
void select_channel(uint8_t channel) {
    uint8_t cmd = 1 << channel;
    i2c_cmd_handle_t cmd_handle = i2c_cmd_link_create();
    i2c_master_start(cmd_handle);
    i2c_master_write_byte(cmd_handle, (TCA9548_ADDR << 1) | I2C_MASTER_WRITE, true);
    i2c_master_write_byte(cmd_handle, cmd, true);
    i2c_master_stop(cmd_handle);
    i2c_master_cmd_begin(I2C_MASTER_NUM, cmd_handle, 1000 / portTICK_PERIOD_MS);
}

// sensor init function
void initialize_veml_device(VEML_Data *data, int channel) {
    esp_err_t init_result = veml7700_initialize(&(data->dev), I2C_MASTER_NUM);
    if (init_result != ESP_OK) {
        ESP_LOGE("VEML7700", "Failed to initialize VEML7700 (Channel %d). Result: %d\n", channel, init_result);
    }
    else{
        ESP_LOGI("VEML7700", "Successfully initialized VEML7700 (Channel %d). Result: %d\n", channel, init_result);
    }
}
//-----------------------------------------------------------------------

//Set stepper task
void stepper_task(float val) {  
    esp_rom_gpio_pad_select_gpio(STEP_PIN);         //selecting CLK pin
    esp_rom_gpio_pad_select_gpio(DIR_PIN);          //selecting DIR pin
    gpio_set_direction(STEP_PIN, GPIO_MODE_OUTPUT); //set CLK pin to output
    gpio_set_direction(DIR_PIN, GPIO_MODE_OUTPUT);  //set DIR pin to output
    //Pull USBC pin up to switch on power to Servos
    esp_rom_gpio_pad_select_gpio(USBC_PIN);
    gpio_set_direction(USBC_PIN, GPIO_MODE_OUTPUT);
    //gpio_set_pull_mode(USBC_PIN, GPIO_PULLUP_ONLY);
    gpio_set_level(USBC_PIN,1);
    val = 1.0/val;
    printf("val after inverse is %.4f\n\n", val);
    val = pow(val,8); // set to 8th power to adjust accurately to sensor values
    // if above 200 reset to 200
    if(val >= 200)
    {
        val = 200;
    }
    current_stepper_val = 0.0;
    ESP_LOGI(TAG, "old horiz value of target is %.4f", target_val_stepper[0]);
    target_val_stepper[0] = ((dir*val) + target_val_stepper[0]);
    ESP_LOGI(TAG, "new horiz value of target is %.4f", target_val_stepper[0]);
    target_val_stepper[1] = ((dir*val) + target_val_stepper[1]);
    printf("\n\nstep size is %.4f\n\n", val);
    for (int i = 0; i < val; i++) { // 200 steps for one revolution
        gpio_set_level(STEP_PIN, 1);
        vTaskDelay(pdMS_TO_TICKS(10)); // Adjust delay
        gpio_set_level(STEP_PIN, 0);
        vTaskDelay(pdMS_TO_TICKS(10)); // Adjust delay
    }
    vTaskDelay(pdMS_TO_TICKS(200)); // Delay between rotations

    esp_rom_gpio_pad_select_gpio(USBA_PIN);
    gpio_set_direction(USBA_PIN, GPIO_MODE_OUTPUT);
    gpio_set_level(USBA_PIN, 1);

    return;
}

// main function
void app_main() {
    esp_rom_gpio_pad_select_gpio(USBA_PIN);
    gpio_set_direction(USBA_PIN, GPIO_MODE_OUTPUT);
    gpio_set_level(USBA_PIN, 1); // power switch **sensor**

    gpio_reset_pin(USBC_PIN);
    esp_rom_gpio_pad_select_gpio(20);
    gpio_set_direction(20, GPIO_MODE_OUTPUT);

    i2c_master_init();
    pca9685_init(I2C_PORT);
    printf("ESP32 Initialized for I2C.\n");


    //----------------------ZIGBEE---------------------------
    esp_zb_platform_config_t config = {
        .radio_config = ESP_ZB_DEFAULT_RADIO_CONFIG(),
        .host_config = ESP_ZB_DEFAULT_HOST_CONFIG(),
    };
    ESP_ERROR_CHECK(nvs_flash_init());
    /* load Zigbee light_bulb platform config to initialization */
    ESP_ERROR_CHECK(esp_zb_platform_config(&config));
    /* hardware related and device init */
    light_driver_init(0);
    //----------------------ZIGBEE---------------------------

    VEML_Data veml_devices[] = {
        { .dev = NULL, .lux = 0, .fc = 0 },  // Data for channel 0 (index 0)
        { .dev = NULL, .lux = 0, .fc = 0 },  // Data for channel 1 (index 1)
        { .dev = NULL, .lux = 0, .fc = 0 },  // Data for channel 2 (index 2)
        { .dev = NULL, .lux = 0, .fc = 0 },  // Data for channel 3 (index 3)
        { .dev = NULL, .lux = 0, .fc = 0 },  // Data for channel 4 (index 4)
    };
    int num_veml_devices = sizeof(veml_devices) / sizeof(VEML_Data);

    for (int i = 0; i < num_veml_devices; i++) { // Start from index 0
        select_channel(i); // Channel index starts from 0
        initialize_veml_device(&veml_devices[i], i); // Initialize VEML device for this channel
    }

    // Initialize timer
    esp_timer_create_args_t timer_args = {
        .callback = timer_isr,
        .name = "software_timer",
        .arg = &veml_devices
    };
    esp_timer_handle_t software_timer;
    esp_timer_create(&timer_args, &software_timer);

    //ZIGBEE-------------------------------------------------
    xTaskCreate(esp_zb_task, "Zigbee_main", 4096, NULL, 5, NULL);
    //ZIGBEE-------------------------------------------------


    //-----------------STARTING VALS FOR MOTORS--------------
    save_value = 600;
    set_servo_angle_loop(600,495, 0);
    ESP_LOGI(TAG, "set sensor servo to 600");

    /*set_servo_angle_loop(510, 510, 1);
    set_servo_angle_loop(600, 600, 2);
    ESP_LOGI(TAG, "set mirror horizontal servo to 520 and vertical to 600");
    vTaskDelay(pdMS_TO_TICKS(1000));

    set_servo_angle_loop(459, 510, 1);
    set_servo_angle_loop(450, 600, 2);
    ESP_LOGI(TAG, "set mirror horizontal servo to 459 and vertical to 450");
    vTaskDelay(pdMS_TO_TICKS(2000));*/
    //-----------------STARTING VALS FOR MOTORS--------------

    // Start timer
    esp_timer_start_periodic(software_timer, 5000000); // 5s timer

    // infinite loop
    while (1) {
        
    }
}
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

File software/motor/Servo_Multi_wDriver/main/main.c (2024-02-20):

#include "stdio.h"
#include "freertos/FreeRTOS.h"          // Operating system library
#include "freertos/task.h"              // task call library
#include "freertos/semphr.h"            // Semaphore API
#include "driver/mcpwm_prelude.h"               // PwM to run servos
#include "driver/i2c.h"                 // i2c library
#include "esp_log.h"                    // esp library

#define SERVO_MIN_PULSEWIDTH 500        // Minimum pulse width in microsecond
#define SERVO_MAX_PULSEWIDTH 2500       // Maximum pulse width in microsecond
#define SERVO_MIN_DEGREE     -135       // Minimum angle
#define SERVO_MAX_DEGREE     135        // Maximum angle >>>270o // rotate counter clockwise   
#define I2C_MASTER_SCL_IO 22            // GPIO pin for I2C clock
#define I2C_MASTER_SDA_IO 21            // GPIO pin for I2C data
#define I2C_MASTER_NUM I2C_NUM_0        // I2C port number
#define PCA9685_ADDR 0x40               // Driver address
#define I2C_MASTER_FREQ_HZ 100000       // !MHz, 1us per tick
#define MODE1   0x00                    // Register mode 1 (standard)  
#define ADDR0   0x06                    // Call first servo register
#define PRESCALE 0xFE                   // prescale bit for servo frequency

//>>> switch to I2C
#define SERVO_TIMEBASE_PERIOD        20000    // 20000 ticks, 20ms

void pca9685_init() {
    i2c_config_t conf;                                          // set up configuartion for I2C
    conf.mode = I2C_MODE_MASTER;                                // Switch to master mode
    conf.sda_io_num = I2C_MASTER_SDA_IO;                        // set SDA pin
    conf.sda_pullup_en = GPIO_PULLUP_ENABLE;                    // pull up SDA
    conf.scl_io_num = I2C_MASTER_SCL_IO;                        // set SCL pin
    conf.scl_pullup_en = GPIO_PULLUP_ENABLE;                    // pull up SCL
    conf.master.clk_speed = I2C_MASTER_FREQ_HZ;                 // 100 kHz clock speed
    conf.clk_flags = 0;                                         // Choosing a source clock <optional>
    i2c_param_config(I2C_MASTER_NUM, &conf);                    // set other parameter to defautl value
    i2c_driver_install(I2C_MASTER_NUM, conf.mode, 0, 0, 0);     // install driver for master, port (0), the rest of param are default

    // set PCA9865 to normal MODE

    i2c_cmd_handle_t cmd = i2c_cmd_link_create();                                                       // create new command
    i2c_master_start(cmd);                                                                              // start command
    i2c_master_write_byte(cmd, (PCA9685_ADDR << 1) | I2C_MASTER_WRITE, true);                           // write to PCA9685
    i2c_master_write_byte(cmd, PRESCALE, true);                                                         // Set to frequency to prescale of 50Hz
    i2c_master_stop(cmd);                                                                               // stop command
    i2c_master_cmd_begin(I2C_MASTER_NUM, cmd, 1000 / portTICK_PERIOD_MS);                                 // delay for 1000 ms
    i2c_cmd_link_delete(cmd);                                                                           // delete command

    // set PWM frequency to prescale value

    cmd = i2c_cmd_link_create();                                                       // create new command
    i2c_master_start(cmd);                                                                              // start command
    i2c_master_write_byte(cmd, (PCA9685_ADDR << 1) | I2C_MASTER_WRITE, true);                           // write to PCA9685
    i2c_master_write_byte(cmd, MODE1, true);                                                            // Set to normal mode
    i2c_master_stop(cmd);                                                                               // stop command
    i2c_master_cmd_begin(I2C_MASTER_NUM, cmd, 1000 / portTICK_PERIOD_MS);                                 // delay for 1000 ms
    i2c_cmd_link_delete(cmd);                                                                           // delete command

}

void set_pwm(uint8_t channel, uint16_t on, uint16_t off) {
    i2c_cmd_handle_t cmd = i2c_cmd_link_create();                                                       // create new command
    i2c_master_start(cmd);                                                                              // start command
    i2c_master_write_byte(cmd, (PCA9685_ADDR << 1) | I2C_MASTER_WRITE, true);                    // write to PCA9685 
    i2c_master_write_byte(cmd, ADDR0 + 4 * channel, true);                                              // switching between servo wil call value
    i2c_master_write_byte(cmd, on & 0xFF, true);                                                        // turn on by masking
    i2c_master_write_byte(cmd, on>>8, true);                                                            // check bit 
    i2c_master_write_byte(cmd, off & 0xFF, true);                                                       // turn off by maskeing
    i2c_master_write_byte(cmd, off>>8, true);                                                           // check bit
    i2c_master_stop(cmd);                                                                               // stop command
    i2c_master_cmd_begin(I2C_MASTER_NUM, cmd, 1000 / portTICK_PERIOD_MS)                                // delay for 1000 ms
    i2c_cmd_link_delete(cmd);                                                                           // delete command
}

void set_servo_angle(uint8_t servo_num, double angle){
    uint16_t pulse_width = SERVO_MIN_PULSEWIDTH + (SERVO_MAX_PULSEWIDTH - SERVO_MIN_PULSEWIDTH)* angle / (SERVO_MAX_DEGREE - SERVO_MIN_DEGREE);

    set_pwm(servo_num, 0, pulse_width);
}
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

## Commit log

2023-10-13 Schematic updates
    [Full_Schematic.sch, PCB_MCU.sch, PCB_Sensors.sch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]
2023-10-14 Schematics updates
    [PCB_MCU.sch, PCB_Sensors.sch, Servo.sch]
2023-10-14 Servo Updated
    [Servo.brd, Servo.sch]
2023-10-20 Hardware and Documents updates
    [CommTower.dwg, Reflector.dwg, Servo.brd]
2023-10-20 CAD updates
    [CommTower.dwg, Reflector.dwg]
2023-10-23 Added regulators and SD Card. Needs major work
    [PCB_MCU.brd, Stepper.sch]
2023-10-24 Updates Schematic
    [Full_Schematic.sch, PCB_MCU.brd, PCB_MCU.sch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]
2023-10-24 Added Silkscreen text, widened approiate traces, added mounting holes
    [Stepper.brd]
2023-10-24 Altium Updates
    [1825910-6.PCBLIB, 1825910-6.SCHLIB, 1N5819HW-7-F.PCBLIB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]
2023-10-24 change folder name
    [1825910-6.PCBLIB, 1825910-6.SCHLIB, 1N5819HW-7-F.PCBLIB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]
2023-10-25 Add Altium Libraries
    [1660.PcbLib, 1660.SchLib, Components - 25.10.23 - 11.19.PcbLib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]
2023-10-26 Add files via upload
    Added SJs and reworked some of the layout
    [Servo_update.brd, Servo_update.sch]
2023-10-26 updated with Dr.Week's advice
    [Stepper.brd, Stepper.sch]
2023-10-27 Updated Schematic with Dr.Week's Advice
    [Servo_update.brd]
2023-10-27 imported from eagle
    [Stepper.PrjPcb]
2023-10-27 imported to altium from Eagle
    [1825910-6.PCBLIB, 1825910-6.SCHLIB, 1N5819HW-7-F.PCBLIB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]
2023-10-27 passing over to binh
    [Stepper.SchDoc]
2023-10-27 Added 3.3Vreg
    [PCB_MCU.PcbDoc, PCB_MCU.SchDoc]
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2023-11-03 Add files via upload
    Updated MCU
    [PCB_MCU.PcbDoc, PCB_MCU.PrjPcb, PCB_MCU.SchDoc]
2023-11-05 Added everything to board, still need to route and check with Dr.Weeks about ESD and protection devices
    [PCB_MCU.PcbDoc, PCB_MCU.PrjPcb, PCB_MCU.SchDoc]
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2023-11-07 Started Routing, corrected a few things on the sch
    [PCB_MCU.PrjPcb, PCB_MCU.SchDoc]
2023-11-07 Did more routing in preparation for Dr. Weeks meeting. Added notes for meeting in discord. Still need to add polygon pours, route/edit pinouts, and change trace size for high-current traces.
    [PCB_MCU.SchDoc]
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2023-11-07 New schematic
    [Sensor_PCB.PcbDoc, Sensor_PCB.PrjPcb, Sensor_PCB.SchDoc]
2023-11-07 Update Servo
    [1N5819HW-7-F.PCBLIB, 1N5819HW-7-F.SCHLIB, AC0805FR-072K2L.PcbLib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]
2023-11-07 Did more routing, upsized traces for power rails, route some of the pintouts. Still needs to upsize the 5v lines and confirm design with Dr.Weeks
    [PCB_MCU.SchDoc]
2023-11-10 Revert ""
    This reverts commit ac9c56ac2cc19b43639679a98ae752f1438a7eaf.
    [PCB_MCU.PrjPcb]
2023-11-14 LPiece Added
    Lpiece
    [Reflector_L_Piece.dwg]
2023-11-17 Nearly finished, routed, added stitching, need to clear errors and send out for fab
    [Servo_PCB.PcbDoc, Servo_PCB.PrjPcb, Servo_PCB.SchDoc]
2023-11-18 Routed board and got to 80% complete. Need to add resistors and jumpers
    [Sensor_PCB.PcbDoc, Sensor_PCB.PrjPcb, Sensor_PCB.SchDoc]
2023-11-18 Add files via upload
    TRYING TO FIX VERSION CONTROL
    [Stepper.PcbDoc]
2023-11-18 Revert ""
    This reverts commit d8623637ee42012c651c6b58d0cd1c96efef24c9.
    [Stepper.PcbDoc]
2023-11-19 Reduced DRC errors to 29
    [Stepper.PcbDoc, Stepper.PrjPcb, Stepper.SchDoc]
2023-11-19 Down to 25 errors, added via stitching on edge of board. Still need to rework the mounting holes
    [Stepper.PcbDoc]
2023-11-19 Reduced number of errors, all remaining errors are due to components themselves
    [Servo_PCB.PcbDoc]
2023-11-20 Fixed the SD card PO
    [PCB_MCU.SchDoc]
2023-11-21 Test for binh, DRC is bugged out
    [Sensor_PCB.PcbDoc, Sensor_PCB.SchDoc]
2023-11-21 Reduced DRC Errors to 99
    [Sensor_PCB.PcbDoc]
2024-01-17 Update 01/16/24
    [Reflector_L_Piece.dwg, Reflector_L_Piece.stl, Servo_Housing1.dwg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]
2024-01-24 Moved USB and Traces down a bit to accomodate sun shade fins
    [Sensor_PCB.PcbDoc]
2024-01-27 CAD Update
    [CommTower.dwg, Mirror_Cutting.dwg, Reflector.dwg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]
2024-01-27 CAD and software update
    [Servo_Motor_MG996R.dwg]
2024-01-27 servo cad update
    [DS3225_Servo.dwg, Servo_Board_Housing.dwg, Servo_Housing_Top.dwg]
2024-01-27 servo update with arm
    [DS3225_Servo.dwg]
2024-01-27 Servo dwg
    [DS3225_Servo.dwg]
2024-01-27 bearing update
    [DS3225_Servo_Bearing.dwg]
2024-01-27 Servo bearing update
    [DS3225_Servo.dwg, DS3225_Servo_Bearing.dwg, DS3225_Servo_Bearing_1.stl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]
2024-01-27 Altium Missing file update
    [DS3225_Servo.dwg, DS3225_Servo_Bearing.dwg, Mirror_Cutting.dxf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]
2024-01-28 Sensor PCB updates
    [Sensor_PCB.PrjPcb]
2024-01-28 servo housing updates
    [Servo_Housing_Bottom.dwg, Servo_Housing_Bottom.stl]
2024-01-28 Servo Housing Top update
    [Servo_Housing_Top.dwg, Servo_Housing_Top.stl]
2024-01-28 L pieces updates
    [Reflector_L_Piece.dwg, Reflector_L_Piece.stl, Sensor_Housing.dwg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]
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2024-01-29 resize cad
    [Servo_Housing_Bottom.dwg]
2024-01-30 Bearing updates
    [DS3225_Servo_Bearing.dwg, DS3225_Servo_Bearing_1.stl, DS3225_Servo_Bearing_2.stl]
2024-01-30 bearing stl update
    [DS3225_Servo_Bearing_1.stl, DS3225_Servo_Bearing_2.stl]
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2024-02-05 Add files via upload
    Cv_Axle Update
    [CV_Axle_V2.stl]
2024-02-05 bearing and servo housing
    [DS3225_Servo_Bearing.dwg, DS3225_Servo_Bearing_1.stl, Servo_Housing_Bottom.dwg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]
2024-02-05 Add files via upload
    Changed CV_Axle diameter from 24.75mm to 25.5 mm
    [CV_Axle_V2_.stl]
2024-02-06 servo housing update
    [Servo_Housing_Bottom.dwg, Servo_Housing_Bottom.stl]
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2024-02-07 design update
    [DS3225_Servo_Bearing.dwg, Servo_Housing_Bottom.dwg, Servo_Housing_Bottom.stl]
2024-02-07 remove files
    [CV_Axle.stl, CV_Axle_V1.stl, CV_Axle_V2.stl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]
2024-02-08 cad changes
    [Gear_for_Stepper(1).stl, Gear_for_Stepper.stl, Reflector_L_Piece.dwg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]
2024-02-15 Remove placeholders, add astromsg project
    [partitions.csv]
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2024-02-19 changed io8&9 and added jumpers
    [PCB_MCU.SchDoc]
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2024-02-22 Add files via upload
    added stand for the mirror tower turntable
    [Stand.stl]
2024-02-23 Add files via upload
    updated stand to make it printable
    [STAND2.stl, stand1.stl]
2024-02-24 Revert "Update PCB_MCU.SchDocPreview"
    This reverts commit ddec6d07e2fb772a69af23b70bcde731b64560f2.
2024-02-24 Revert ""
    This reverts commit 31b8cfdc3627c0a10d7378ba0c8c8245825f1724.
    [StepperV2.PrjPcb]
2024-02-24 Revert ""
    This reverts commit 0a18cf6965cb90f89b2af8d74de933828272ad35.
    [PCB_MCU.PrjPcb, PCB_MCU.SchDoc, SSwitch.PcbLib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]
2024-02-24 Revert "SCHEMATIC"
    This reverts commit b3244c10bdc3b370953aed1d92168c0c535bb831.
    [0.1uFCAP.PcbLib, 0.1uFCAP.SCHLIB, 12kOHM.PcbLib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]
2024-02-24 Revert "Revert "SCHEMATIC""
    This reverts commit 2732cb36103b64c9210c05b73c3fbde493747707.
    [0.1uFCAP.PcbLib, 0.1uFCAP.SCHLIB, 12kOHM.PcbLib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]
2024-02-24 Revert "Revert """
    This reverts commit 8e956d1836c0f8c36de412ee7d657c7c1d2db0cf.
    [PCB_MCU.PrjPcb, PCB_MCU.SchDoc, SSwitch.PcbLib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]
2024-02-24 Revert "Revert """
    This reverts commit 58cbc57fabd00ab80dc60cc66da1a14e84a25dc3.
    [StepperV2.PrjPcb]
2024-02-24 Revert "Revert "Update PCB_MCU.SchDocPreview""
    This reverts commit 89693c5361c2808f3b457fc1f309fa40f13faff4.
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2024-02-24 Messaging real + converter js
    [partitions.csv]
2024-02-29 MCU Board
    Increased trace width of USBs
    updated schematic
    [PCB_MCU.SchDoc]
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2024-03-14 updated astrocom code with mirror in vertical direction
    [partitions.csv]
2024-04-03 Add conference paper to website
    [BOM.xlsx]
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

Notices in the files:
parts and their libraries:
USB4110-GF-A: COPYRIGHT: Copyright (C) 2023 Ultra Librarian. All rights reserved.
